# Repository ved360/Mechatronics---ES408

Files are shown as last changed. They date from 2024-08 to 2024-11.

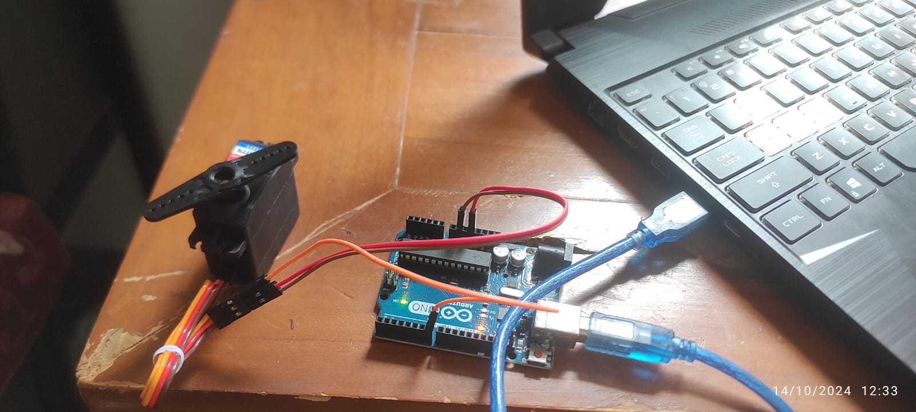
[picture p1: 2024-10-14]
Servo Testing/WhatsApp Image 2024-10-14 at 12.35.41_b7d5177f.jpg

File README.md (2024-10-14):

# Pick and Place Robot

**Challenge:** In the fast-paced industrial sector, time efficiency is a critical driver of success, directly influencing both production and profitability. Streamlining intermediate processes can lead to significant increases in output, allowing companies to meet growing demand and stay competitive. A prominent opportunity for such optimization has emerged within a tea bag manufacturing company, particularly in its packaging division. Currently, tea bags are manually packed into retail boxes—a labor-intensive process that slows down overall production. To meet rising market demands and boost efficiency, the company is looking to automate this packaging process. Implementing an automated solution would not only reduce manual effort but also accelerate production timelines, enhance consistency, and increase output, positioning the company to capture greater market share and reduce operational costs.

 

**Proposed Solution:** To address this challenge, we are introducing a solution: our Pick and Place Robot, specifically designed to automate the tea bag packaging process. This PRR (Prismatic-Revolute-Revolute) manipulator is engineered to significantly accelerate packaging, enhancing both speed and efficiency. The robot features a Prismatic joint that controls the vertical movement, ensuring precise and smooth handling. Additionally, its two Revolute joints are designed to position the gripper at the end-effector, enabling it to align perfectly with the tea bags for seamless operation. By automating the packaging process, our robot is capable of outpacing current manual systems, delivering faster, more consistent results. This solution not only reduces human labor but also drives greater productivity, offering the company a powerful tool to optimize operations and meet increasing demand with ease.



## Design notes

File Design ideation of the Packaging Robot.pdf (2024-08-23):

## Design ideation of the Packaging Robot

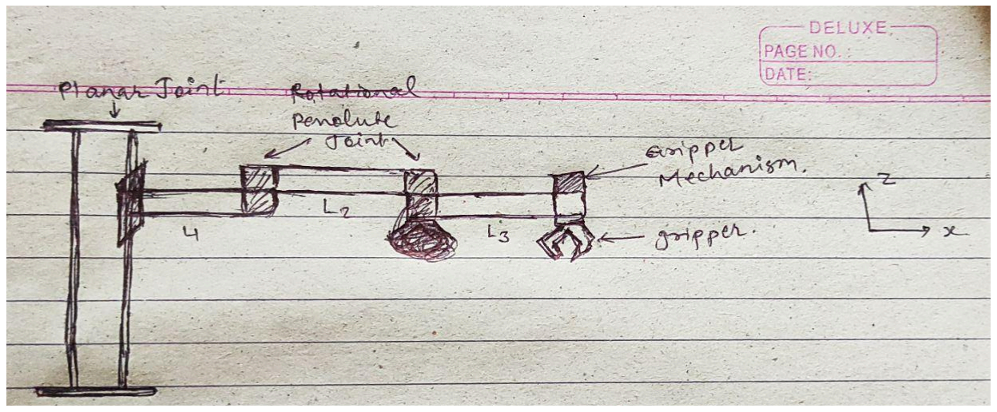
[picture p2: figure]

This is the basic design for the robotic arm to pick and place. It will contain PRR joints, and a pneumatic gripper will be installed on the last link.

-> Design Ideation for P joint:

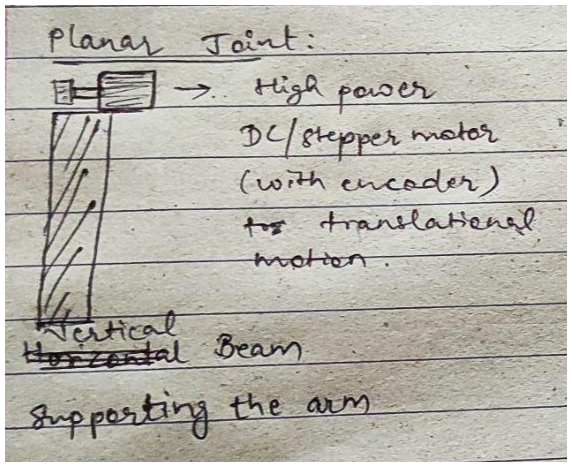
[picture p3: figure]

A verticle beam will support the whole link system, and the translation in the Z axis will be done with the help of a belt mechanism driven by a high-power DC/Stepper motor.

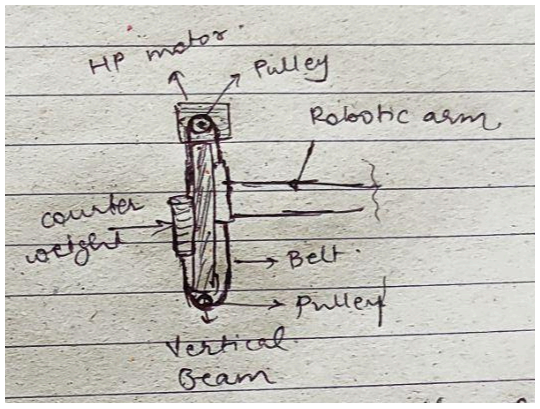
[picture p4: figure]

A counterweight equal to the weight of the links will be used to cancel out the torque applied by the links on the motor. This way, the motor will not be required to apply constant torque to keep the link at a certain Z.

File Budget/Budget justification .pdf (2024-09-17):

Gripper Mechanism

- Ecoflex 00-20 Super Soft Silicone (A and B) -: We are using Ecoflex 00-20 Super Soft Silicone to make the soft fingers of the gripper for our pick and place operation. The material's properties are ideal for creating flexible, durable, and gentle gripper fingers that can handle delicate and irregularly shaped objects effectively.
- The AUTO Addict 12V DC Air Compressor Pump -: being utilized in our project to provide the necessary positive and negative pressure required to operate the silicone soft fingers of the gripper. This compressor enables the inflation and deflation of the fingers, allowing them to grip and release objects effectively.
- The 3-Way 2-Position Pneumatic Solenoid Valve (12V) -: used in our project to control the direction of air flow to the silicone soft fingers of the gripper. This valve is essential for switching between positive (inflation) and negative (deflation) pressure, enabling the gripper to effectively pick up and release objects.
- The inner tube -: used to transfer air pressure from the air compressor to the silicone soft fingers of the gripper. These tubes play a crucial role in delivering both positive and negative pressure to the gripper fingers, enabling them to inflate and deflate for gripping and releasing objects.
- 1/4 inch Air Hose T Connector 4PCS -: used to create connections between the air tubes and various components in the pneumatic system, such as the air compressor, solenoid valves, and gripper finger

Motor Torque calculation:

3d printing Material PLA density = 1.24gm/cm³ Volume of Link 1 = 307.2 cm³
Volume of Link 2 = 206.8 cm³
Mass of Link 1 = 380.9 gm
Mass of Link 2 = 256.5 gm
Mass of Servo Motor = 48 gm

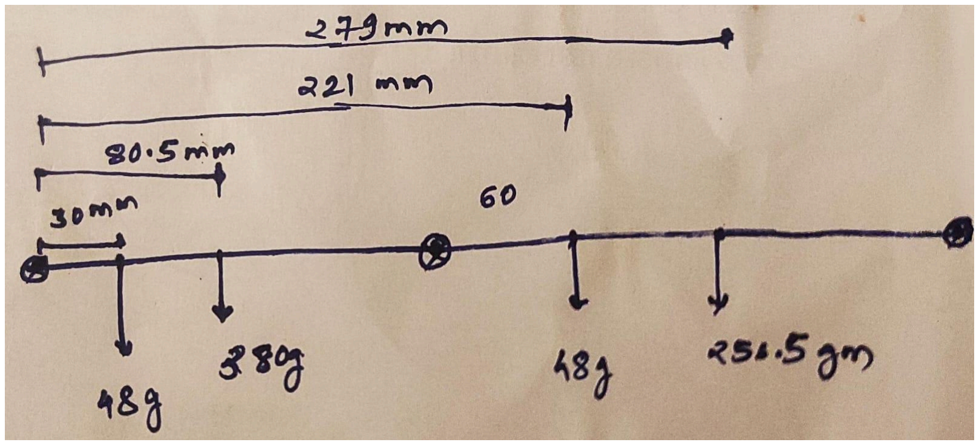
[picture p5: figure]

Moment = (48*30 + 380*80.5 + 48*221 + 250.5*279) * g * 10

-6
= (112527.5) * 9.8 * 10

-6
= 1.102769 Nm
= 11.245 kg-cm

So, after going through some servo motor models we have finalized with torque value to be 14 kg-cm.

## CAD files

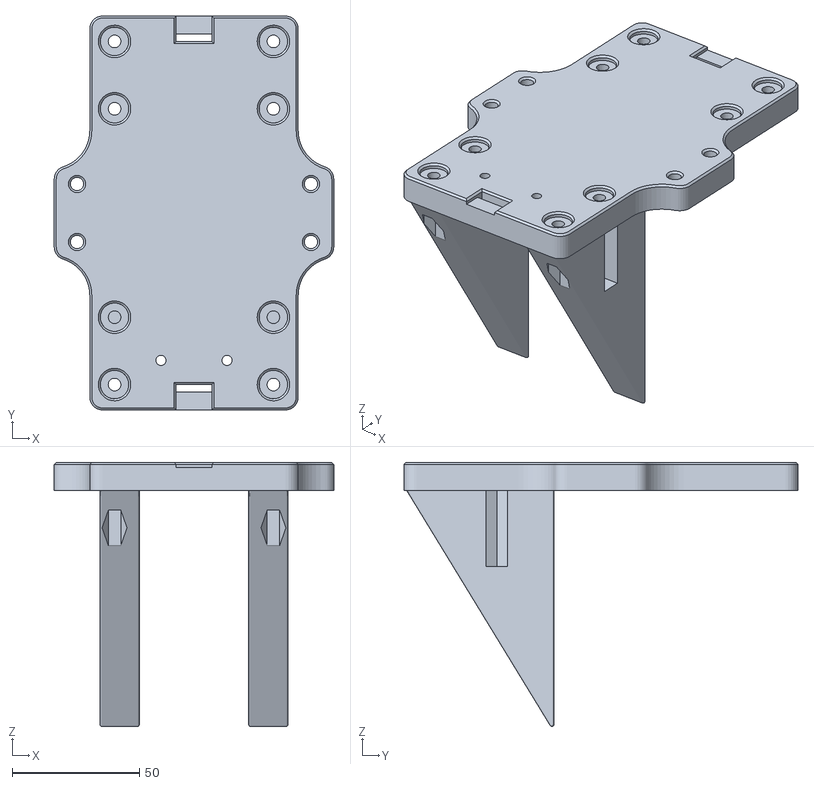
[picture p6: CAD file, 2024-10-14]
3D Print Files/Roller Plate/SCARA - Z Axis Wheel drive Assembly_40mmExtusionV_Wheel v1.stl
110.0 x 155.0 x 104.0

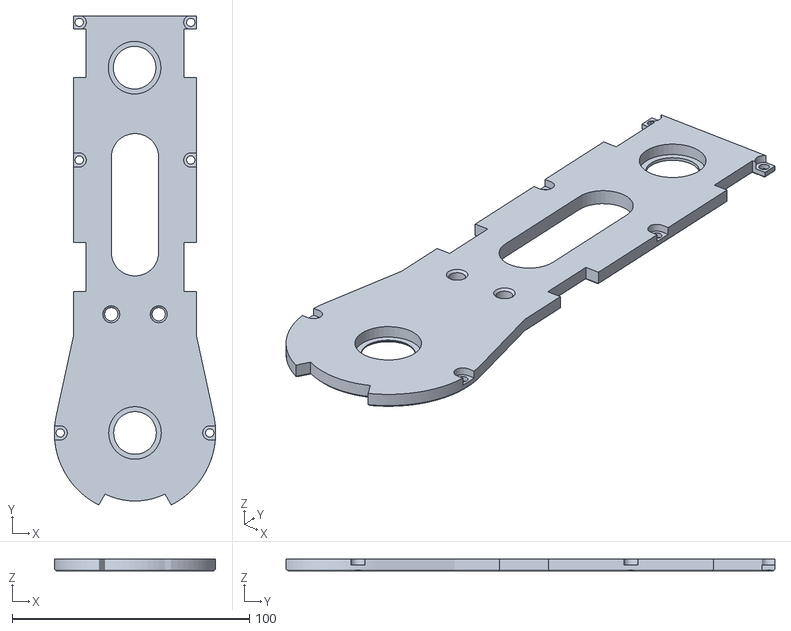
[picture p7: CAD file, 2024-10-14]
3D Print Files/Last Link/SCARA - Last Link Body 1 v2.stl
68.0 x 206.1 x 5.00

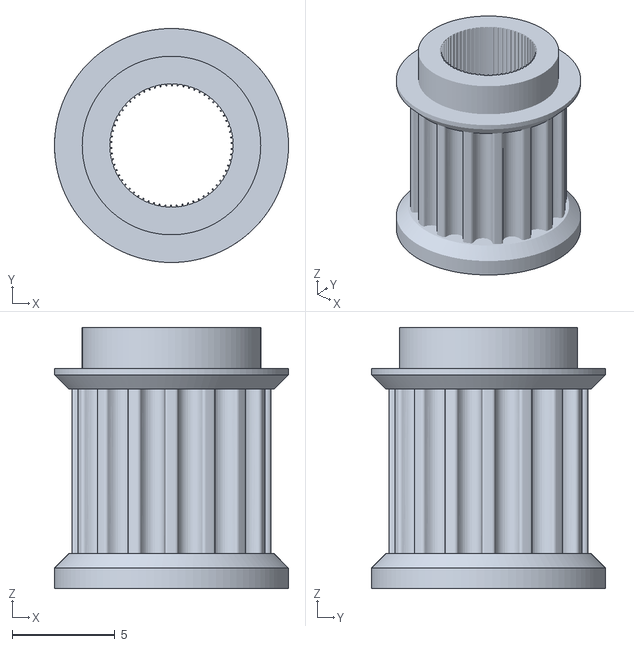
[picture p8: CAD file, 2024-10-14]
3D Print Files/SCARA - Short-Flat 16t TimingBeltPulley for M1 v1.stl
11.4 x 11.4 x 12.7

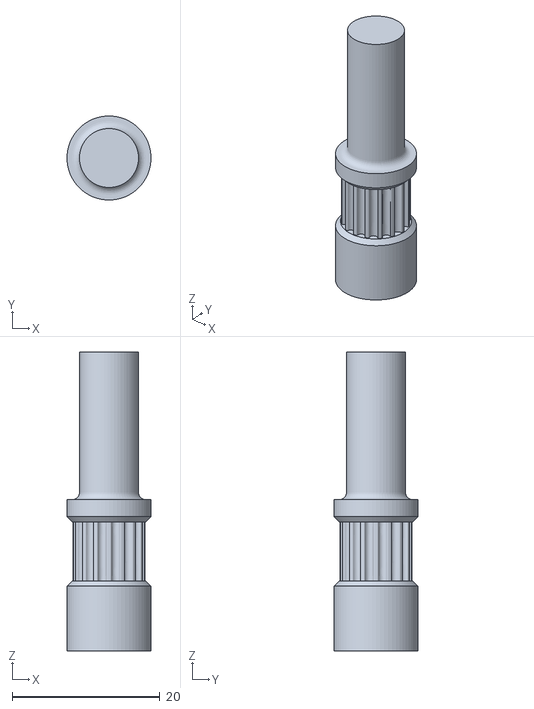
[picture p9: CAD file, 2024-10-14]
3D Print Files/Second Joint/SCARA - Arm Segment With Servo Motor Design 2 Coupler v1.stl
11.4 x 11.4 x 40.5

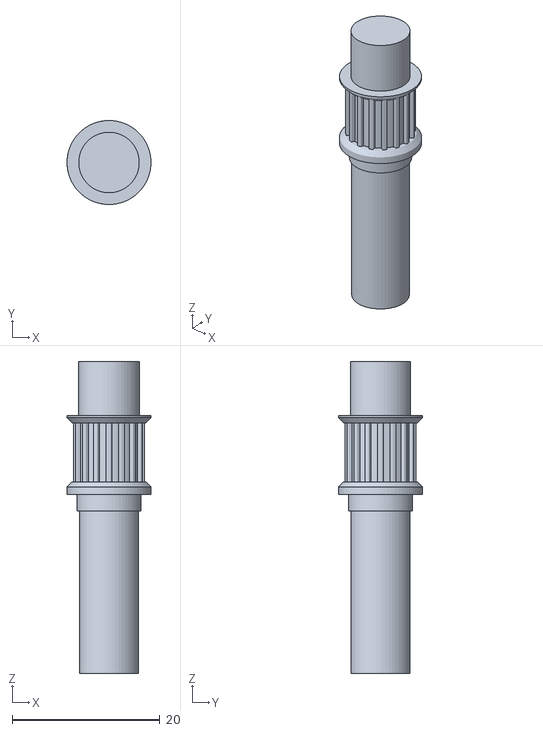
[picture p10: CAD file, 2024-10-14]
3D Print Files/Z axiis/SCARA - Z-Axis Coupler's coupler v2.stl
11.4 x 11.4 x 42.3

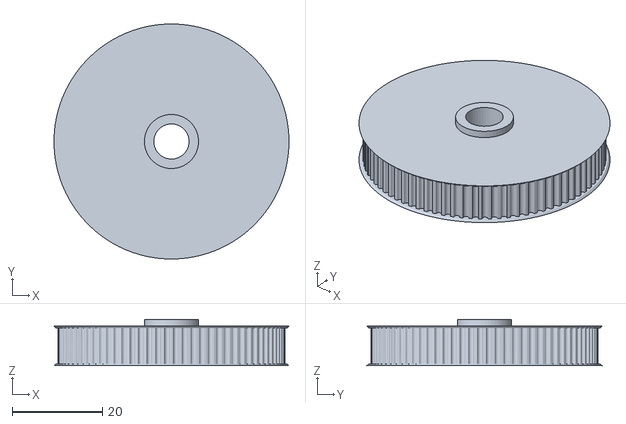
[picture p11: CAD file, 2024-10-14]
3D Print Files/Last Link/SCARA - Last Link_GT2_80t_TimingBeltPulley v2.stl
52.1 x 52.1 x 10.3

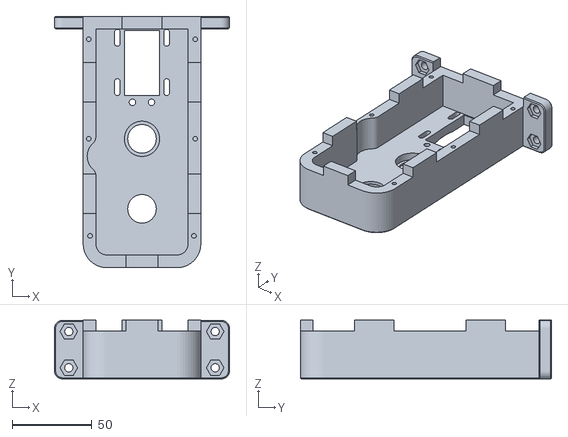
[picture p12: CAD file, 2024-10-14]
3D Print Files/Second Joint/SCARA - Arm Segment With Servo Desing 2 (Body 1) v2.stl
110.0 x 158.0 x 37.0

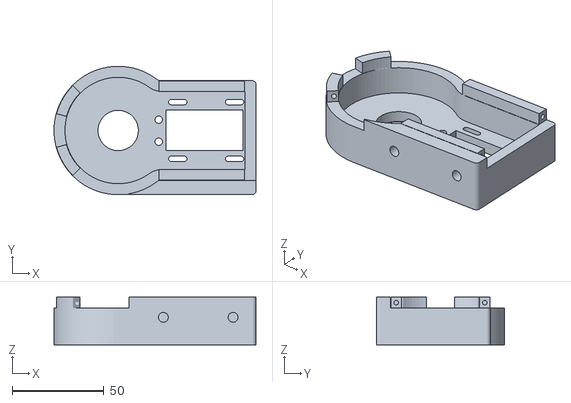
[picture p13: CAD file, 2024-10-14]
3D Print Files/Z axiis/SCARA - Z-axis Gearbox (Body 1) v2.stl
110.1 x 70.0 x 26.0

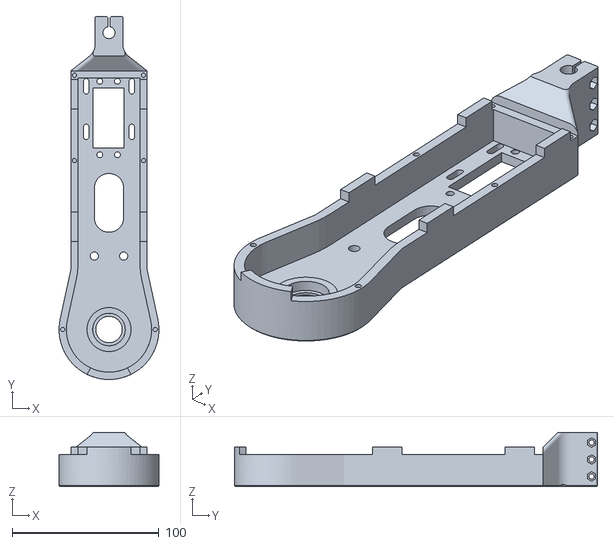
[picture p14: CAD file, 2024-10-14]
3D Print Files/Last Link/SCARA - Last Link Body 2 v3.stl
68.0 x 247.0 x 37.0

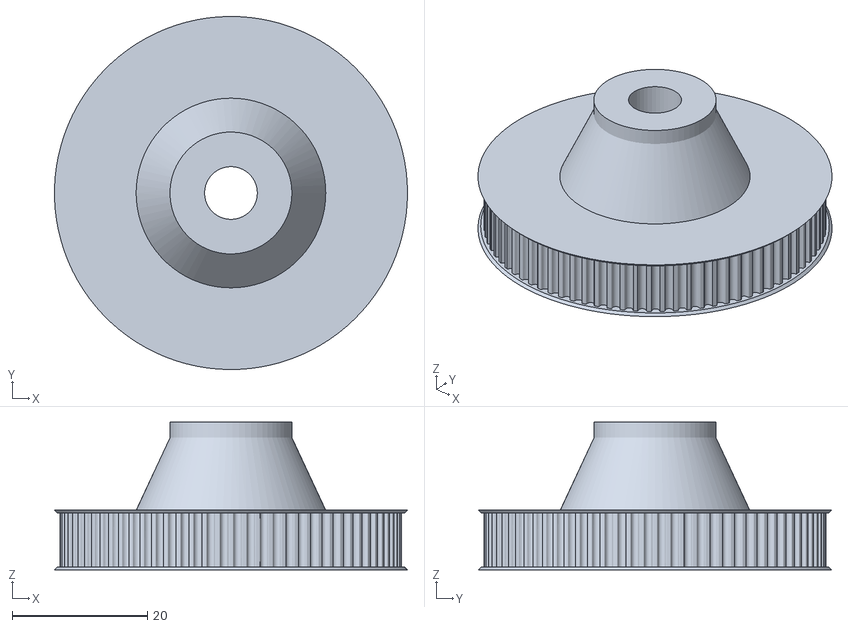
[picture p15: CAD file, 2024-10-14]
3D Print Files/Second Joint/SCARA - Arm Segment_ExtendedGT2_80t_TimingBeltPulley v2.stl
52.1 x 52.1 x 21.8

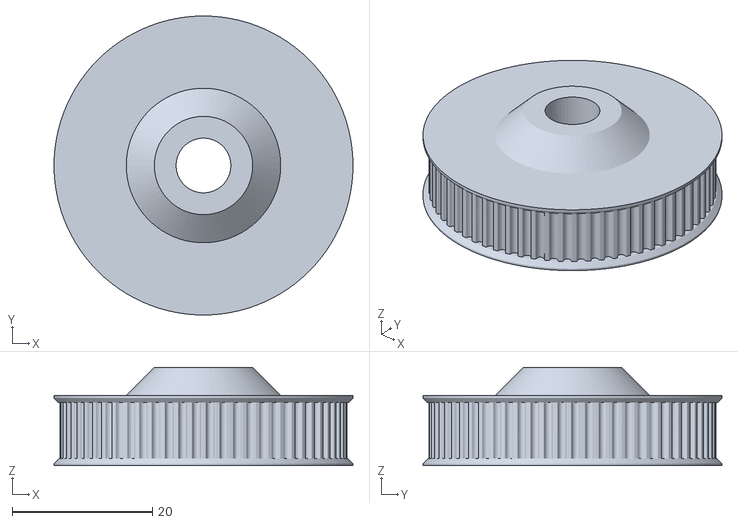
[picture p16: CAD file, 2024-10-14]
3D Print Files/Z axiis/SCARA - Z-axis Assem_Z-AxisPulley v2.stl
42.6 x 42.6 x 14.0

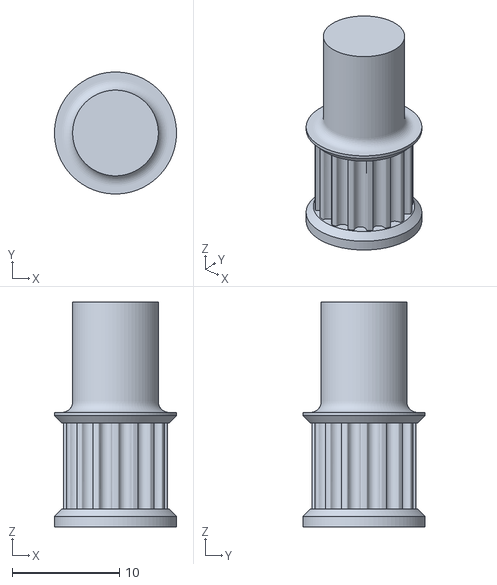
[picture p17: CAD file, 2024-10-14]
3D Print Files/Last Link/SCARA - Last Link Coupler v1.stl
11.4 x 11.4 x 21.0

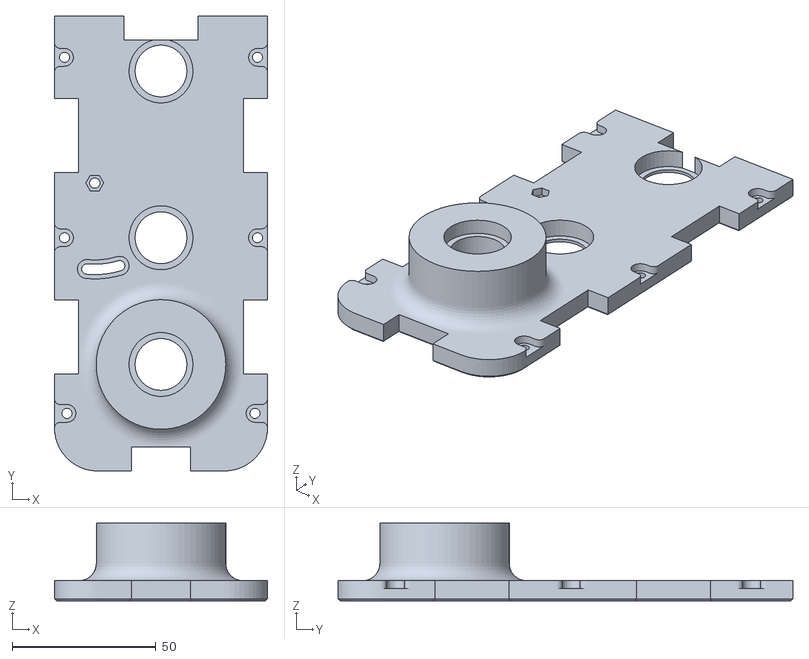
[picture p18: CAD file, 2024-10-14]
3D Print Files/Second Joint/SCARA - Arm Segment With Servo Desing 2 (Body 2) v2.stl
74.0 x 158.0 x 27.0

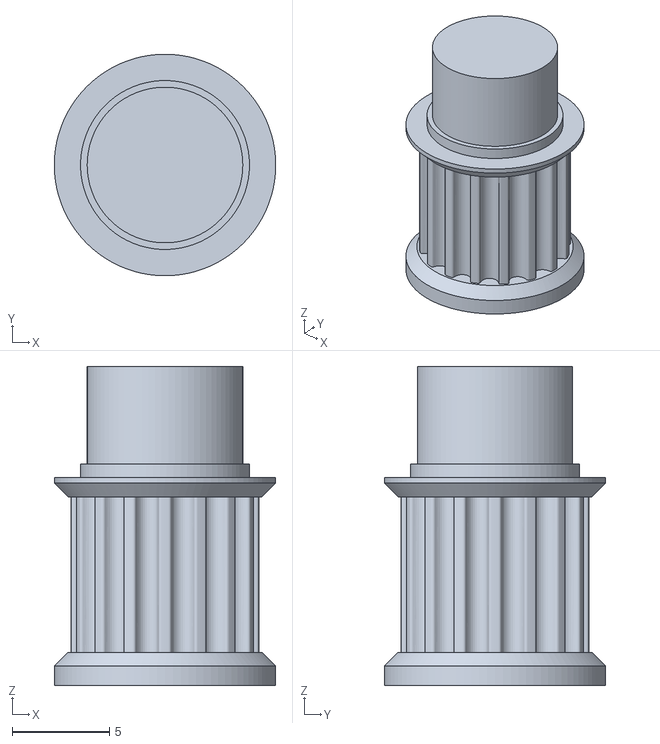
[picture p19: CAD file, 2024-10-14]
3D Print Files/Z axiis/SCARA - Z Axis ServoCoupler v2.stl
11.4 x 11.4 x 16.4

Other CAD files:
3D Print Files/Z axiis/SCARA - Z-axis Gearbox (Body 2) v2.stl
3D Print Files/Z axiis/SCARA - Z-axis Assem_605zz idler v1.stl
3D Print Files/Z axiis/SCARA - Z-axis Assem_608Idler v1.stl

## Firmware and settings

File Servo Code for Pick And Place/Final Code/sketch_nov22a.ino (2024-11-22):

#include <Wire.h>
#include <Adafruit_PWMServoDriver.h>

// Create an instance of the PWM driver
Adafruit_PWMServoDriver pwm = Adafruit_PWMServoDriver();

// Set the pulse length parameters
#define SERVOMIN  150   // Minimum pulse length for a 0-degree angle
#define SERVOMAX  600   // Maximum pulse length for a 180-degree angle
// #define SERVONUM  0     // Servo motor channel on the PWM board (0-15)

void setup() {
  Serial.begin(9600);
  Serial.println("Starting servo control");

  pwm.begin();
  pwm.setPWMFreq(60);  // Set the PWM frequency to 60 Hz for standard servos
}

void setServoAngle(uint8_t servo, float angle) {
  // Map the angle (0-180) to the pulse length range
  uint16_t pulselength = map(angle, 0, 180, SERVOMIN, SERVOMAX);
  pwm.setPWM(servo, 0, pulselength);
}

void loop() {
  // Test: Move servo to 0 degrees
  setServoAngle(4, 90);
  delay(1000);

  setServoAngle(1, 90);
  delay(1000);

  setServoAngle(1, 180);
  delay(1000);

  setServoAngle(4, 180);
  delay(1000);

  setServoAngle(4, 90);
  // delay(1000);

  setServoAngle(1, 90);
  delay(1000);

  setServoAngle(1, 0);
  delay(1000);

  setServoAngle(4, 180);
  delay(1000);

  setServoAngle(4, 90);
  // delay(1000);

  setServoAngle(1, 90);
  delay(1000);

}
